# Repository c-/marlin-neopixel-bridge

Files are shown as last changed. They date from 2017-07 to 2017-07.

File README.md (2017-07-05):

# marlin-neopixel-bridge

Using an ATtiny85 to bridge between Marlin firmware and Neopixel LED's
simply by emulating the minimal amount of BlinkM I2C commands needed to
show some colours.

Pictures and more writing here: http://imgur.com/a/qqFzk

Arduino code is in ATtiny85_BlinkM_Neopixel_Bridge/. You need the ATTinyCore,
TinyWireS, and Adafruit_NeoPixel libraries installed.

KiCad schematic and pcb layout are included. 

The BOM is:

 * ATtiny85 (DIP8 with socket)
 * .1uF capacitor
 * 300-500 ohm resistor (I used 470)
 * one larger cap for the Neopixels (100uF seems fine)
 * 2 4.7k ohm resistors for the I2C pullups
 * headers, wires, etc. I used pin headers and Dupont connectors

The install is straightforward (I assume you know what tools are needed and
how to use them):

 1. in Marlin's Configuration.h uncomment the line "#define BLINKM", compile
and upload. It shouldn't break anything if the I2C device isn't connected
yet.

 2. find or create a mount to put your Neopixel strips where you want them.

 3. (optional, but recommended) breadboard the circuit, program the AVR,
 connect to the I2C header on the controller board (on RAMPS, that's
 just above the endstops). Test it with M150 Rxx Uxx Bxx G-codes (note
 that the color operators appear to be case-sensitive).

 4. etch a PCB or solder up a perf board. Or solder the pieces together and
 cover it all with hot glue and tape. It's your printer.

 5. mount it and enjoy the shiny lights.

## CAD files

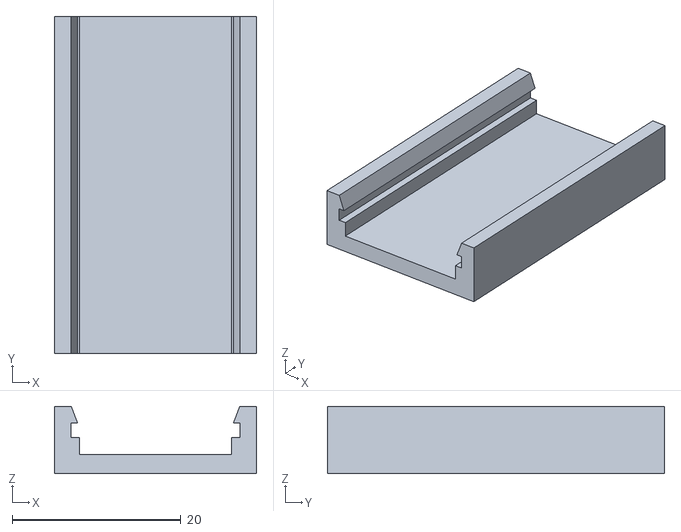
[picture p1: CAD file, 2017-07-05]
models/Marneo Holder.stl
24.0 x 40.0 x 8.00

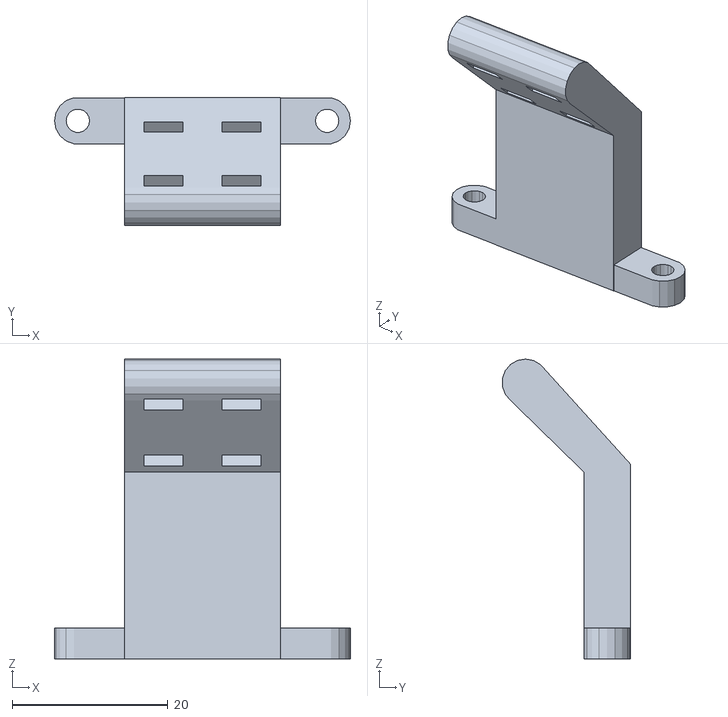
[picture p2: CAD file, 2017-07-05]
models/i3v LED strip mount.stl
38.0 x 16.5 x 38.5

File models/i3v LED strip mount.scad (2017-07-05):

clipw = 10.5;
clipt = 1.5;
clipl = 25;
screwsp = 32;
screwd = 3;

w = screwsp-screwd*4;

$fn=18;

difference() {
   union() {
      hull() {
         translate([-screwsp/2,0,0]) cylinder(d=screwd*2, h=4);
         translate([screwsp/2,0,0]) cylinder(d=screwd*2, h=4);
      }
      translate([-w/2,-screwd,0]) cube([w, screwd*2, clipl]);
      hull() {
         translate([-w/2,-screwd,clipl-1]) cube([w, screwd*2, 1]);
         translate([-w/2,-clipw,clipl+clipw])
            rotate([0,90,0]) 
            cylinder(d=screwd*2,h=w);
      }
   }
   union() {
      translate([-screwsp/2,0,0]) cylinder(d=screwd, h=5);
      translate([screwsp/2,0,0]) cylinder(d=screwd, h=5);
      
      // zip tie holes
      translate([w/2-5,-screwd*2,clipl-1])
         rotate([-45,0,0]) cube([5,2,clipw*2],center=true);
      translate([-w/2+5,-screwd*2,clipl-1])
         rotate([-45,0,0]) cube([5,2,clipw*2],center=true);
      translate([w/2-5,-screwd*2,clipl+clipw+3])
         rotate([-45,0,0]) cube([5,2,clipw*2],center=true);
      translate([-w/2+5,-screwd*2,clipl+clipw+3])
         rotate([-45,0,0]) cube([5,2,clipw*2],center=true);
   }
}

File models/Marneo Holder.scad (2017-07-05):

bw = 20;
bl = 40;
ht = 8;
bt = 1.7;
w = 2;
o = 1.6;

difference() {
   cube([bw+w*2,bl,ht]);
   union() {
      translate([w,0,ht-bt-2]) cube([bw,bl+1,bt]);
      translate([w*1.5,0,ht-bt-4]) cube([bw-w,bl+1,ht]);
      hull() {
         translate([w,0,ht]) cube([bw,bl+1,0.1]);
         translate([w+o/2,0,ht-2.1]) cube([bw-o,bl+1,bt]);
      }
   }
}

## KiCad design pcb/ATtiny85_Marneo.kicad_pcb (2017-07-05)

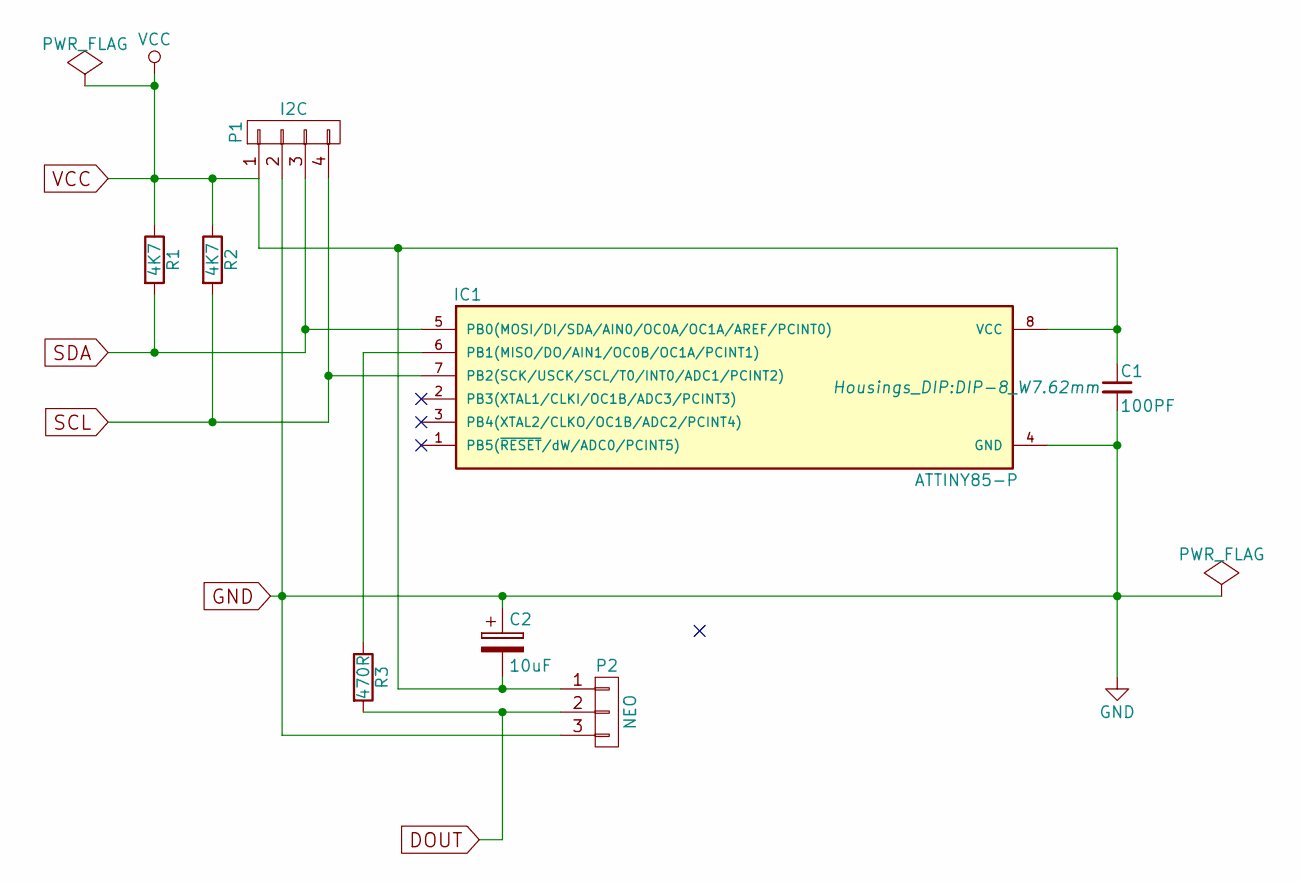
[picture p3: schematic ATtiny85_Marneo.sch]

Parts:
C1: 100PF; C_Disc_D3_P2.5
C2: 10uF; C_Radial_D5_L11_P2
IC1: ATTINY85-P; DIP-8_W7.62mm
P1: I2C; Socket_Strip_Straight_1x04
P2: NEO; Socket_Strip_Straight_1x03
R1, R2: 4K7; Resistor_Horizontal_RM7mm
R3: 470R; Resistor_Horizontal_RM7mm

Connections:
DOUT: P2.2, R3.2
GND: C1.2, C2.1, IC1.4 (GND), P1.2, P2.3
unnamed: IC1.6 (PB1(MISO/DO/AIN1/OC0B/OC1A/PCINT1)), R3.1
SCL: IC1.7 (PB2(SCK/USCK/SCL/T0/INT0/ADC1/PCINT2)), P1.4, R2.2
SDA: IC1.5 (PB0(MOSI/DI/SDA/AIN0/OC0A/OC1A/AREF/PCI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), P1.3, R1.2
VCC: C1.1, C2.2, IC1.8 (VCC), P1.1, P2.1, R1.1, R2.1

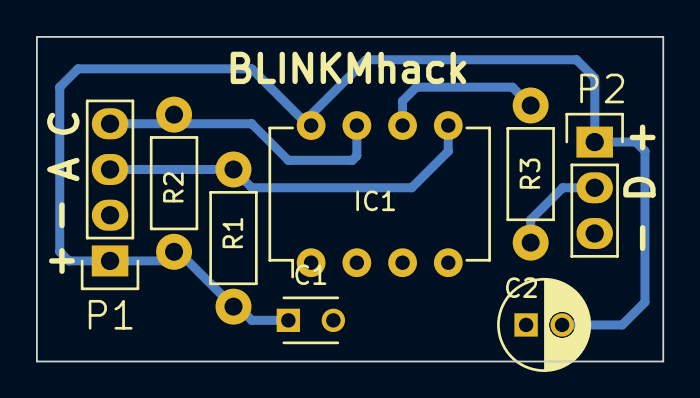
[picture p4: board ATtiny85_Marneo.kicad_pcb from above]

Board: 2 copper layers, 34.8 x 18.0 mm, 8 parts (0 on the bottom side), 6 nets.

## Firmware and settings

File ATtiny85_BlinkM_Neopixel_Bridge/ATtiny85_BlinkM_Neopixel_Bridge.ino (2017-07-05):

#include "TinyWireS.h"
#include <Adafruit_NeoPixel.h>
#ifdef __AVR__
  #include <avr/power.h>
#endif

// Simple bridge between Marlin's BlinkM RGB LED output and a Neopixel (compat) strip.
// Note that this is *not* a general purpuse BlinkM emulator, although it probably could be
// given time. If Marlin changes the BlinkM command set that it uses this will have to be
// adapted.
//
// Wiring:
// ATtiny85 power/GND/caps as usual
// PB0 to RAMPS SDA (w/ 4.7k pullup)
// PB1 to Neopixel data (through ~470R)
// PB2 to RAMPS SCL (w/ 4.7k pullup)

#define I2C_SLAVE_ADDR 0x09

#define LEDPIN 1
#define NLEDS 4

Adafruit_NeoPixel strip = Adafruit_NeoPixel(NLEDS, LEDPIN, NEO_GRB + NEO_KHZ800);

static inline void setStrip(uint32_t c) {
  for( int i = 0; i < strip.numPixels(); i ++ ) {
    strip.setPixelColor(i, c);
  }
  strip.show();
}

void setup() {
  #if defined (__AVR_ATtiny85__)
    if (F_CPU == 8000000) clock_prescale_set(clock_div_1);
    if (F_CPU == 16000000) clock_prescale_set(clock_div_1);
  #endif

  strip.begin();
  setStrip(strip.Color(255,255,255));

  TinyWireS.begin( I2C_SLAVE_ADDR );
}

void loop() {
  // we could probably just continuously block on TinyWireS.receive(), but that's
  // kind of bad form.
  if( TinyWireS.available() ) {
    byte cmd = TinyWireS.receive();
    switch(cmd) {
      case 'n': {
        byte r = TinyWireS.receive();
        byte g = TinyWireS.receive();
        byte b = TinyWireS.receive();
        setStrip( strip.Color(r,g,b) );
        break;
      }
      default:
        // 'o' is the only other command we should expect
        break;
    }
  }
  delay(1);
}

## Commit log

2017-07-05 add the files
    [ATtiny85_Marneo.kicad_pcb, ATtiny85_Marneo.sch]
2017-07-05 add STL/SCAD models
    [Marneo Holder.scad, Marneo Holder.stl, i3v LED strip mount.scad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]
